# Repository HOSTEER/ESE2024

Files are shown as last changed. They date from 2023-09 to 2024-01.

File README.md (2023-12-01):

# ESE2024
    Emilie Butruille
    Louis Liénart
    Théo Césari
    Victor Lesne
------

Activer doxygen dans les propriétés du projet -> général C/C++, tuto doxygen https://www.youtube.com/watch?v=GC9Xy7nLxyw

Pour importer un projet sur cubeIDE, il faut faire "File" -> "Import" -> "General" -> "Project from Folder or Archive" puis sélectionner le directory (exemple "C:\Users\louis\Desktop\ProjetCubeIDE") et ensuite faire "finish".
Après ça, il faut régénérer des fichiers du code, donc cliquer sur "Device configuration tool Code generation"

Avec GitBash, pour retirer un fichier "add" par erreur faire un "git reset nom_du_fichier", un reset seul retirera tout les add fait.

Convention à avoir pour le stockage des sources :
pour stocker les lib créer faire un dossier source "Prod" avec comme sous-fichier "Inc" et "Src"
Ensuite les ajouter dans "Project" -> "Properties" -> "C/C++ General" -> "Paths and Symbols" -> "add" -> entrer "Prod/Inc" et faire ok.

Pour vérifier qu'une branch est ok, cloner un 2nd repo de la branch et la tester pour vérifier l'absence d'erreurs, sinon ça veut dire qu'il manque un truc au commit.

Ensuite il faut résoudre les conflits entre .cproject ( globalement garder le code du main ); .ioc (globalement fusionner les pins ajoutés et faire gaffe au pin, en double) et enfin le main.c ( où il faut fusionner )

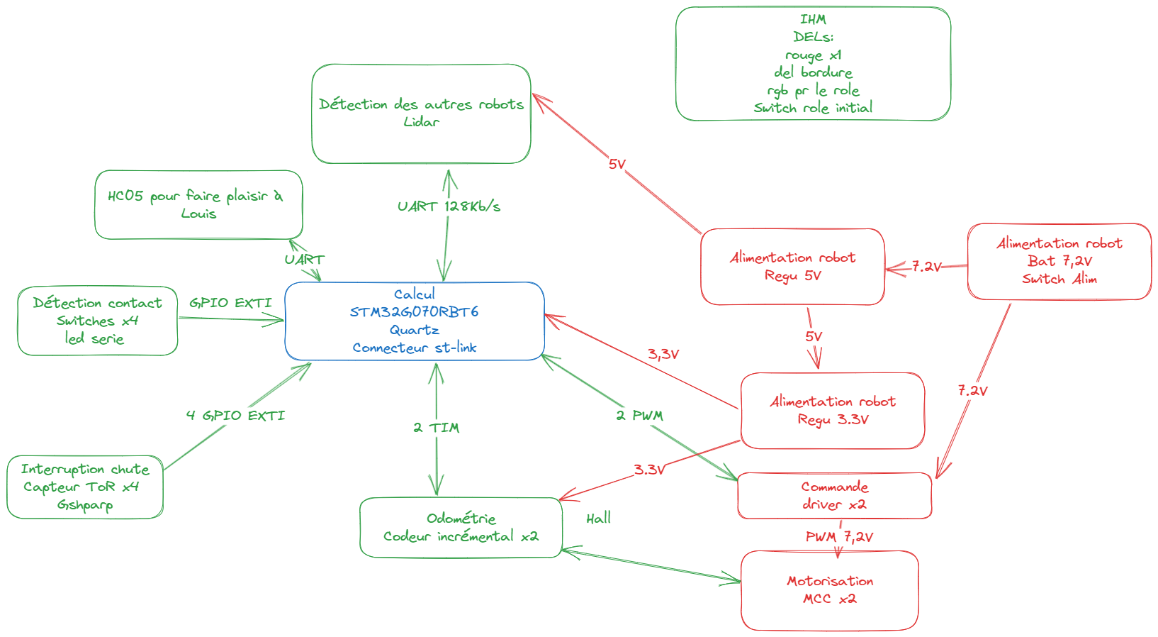
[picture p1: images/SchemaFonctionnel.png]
Schema fonctionnel du robot chat


conso moyenne 300 mA

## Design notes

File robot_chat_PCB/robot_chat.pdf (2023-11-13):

robot_chat

Ref | Qnty Value
C302, | 1 470uF
D201, D202, D203, D204, D205, D206, | 6 ~
D301, | 1 ~
D302, | 1 1N4148
D303, D304, D602 | 3 3.3V, 5V, Status
D501, D604, D605 | 3 Bump, Debug_1, Debug_2
D601, D603 | 2 Border_Detect, Error
F301, | 1 10A
IC401, IC402, | 2 NCS199A3RSQT2G
J301, J501 | 2 Bat,Bump
J401, J402 | 2 L_Mot,R_Mot
J502, | 1 Lidar
J503, J504 | 2 B_Detect, F_Detect
J601, | 1 BT
L201, | 1 2.2u
L301, | 1 4.7uH
SW201, SW601, SW602 | 3 RST, Start, Status
SW301, | 1 SW_SPDT_MSM
U201, | 1 STM32G070RBTx
U301, | 1 MP1475DJ-LF-P
U302, | 1 MIC5317-3.3xM5
U401, U402, | 2 ZXBM5210-SP
U501, | 1 LSM6DSM
Y201, | 1 16MHz

Footprint | ref farnell

Capacitor_SMD:CP_Elec_10x10.5

Diode_SMD:D_SOD-923 | 3702487RL
Diode_SMD:D_SMB | 3373187RL

Diode_SMD:D_SOD-323F

LED_SMD:LED_0603_1608Metric | 3796304
LED_SMD:LED_0603_1608Metric | 3796315
LED_SMD:LED_0603_1608Metric | 3796316
Fuse:Fuse_1206_3216Metric | 3564732
Package_TO_SOT_SMD:SOT-363_SC-70-6 | 2981170
Connector_JST:JST_XH_S2B-XH-A_1x02_P2.50mm_Horizontal | 1516289
Connector_JST:JST_XH_S6B-XH-A_1x06_P2.50mm_Horizontal | 1516294
Connector_JST:JST_XH_S8B-XH-A_1x08_P2.50mm_Horizontal | 1516296
Connector_JST:JST_XH_S3B-XH-A_1x03_P2.50mm_Horizontal | 1516290
Connector_PinSocket_2.54mm:PinSocket_1x06_P2.54mm_Horizontal | 2827951
Inductor_SMD:L_0603_1608Metric | 3666006

Inductor_SMD:L_1008_2520Metric

Button_Switch_SMD:SW_SPST_B3U-1000P | 1333652
472121020421:Toggle_Switch | 4244949

Package_QFP:LQFP-64_10x10mm_P0.5mm

Package_TO_SOT_SMD:TSOT-23-8

Package_TO_SOT_SMD:SOT-23-5

Package_SO:SOIC-8-1EP_3.9x4.9mm_P1.27mm_EP2.62x3.51mm_ThermalVias

Package_LGA:LGA-14_3x2.5mm_P0.5mm_LayoutBorder3x4y | 2664522

Crystal:Crystal_SMD_EuroQuartz_MT-4Pin_3.2x2.5mm

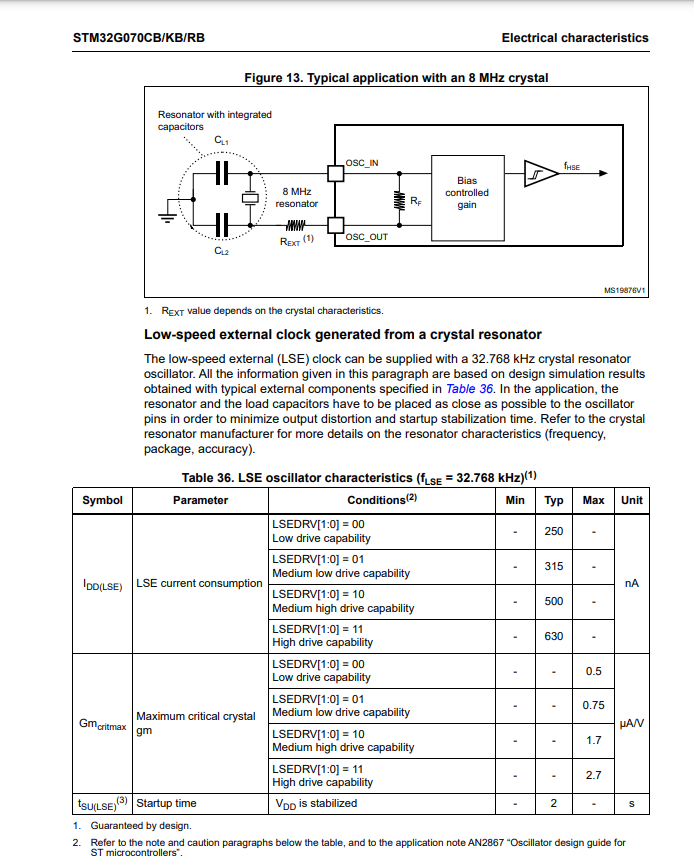
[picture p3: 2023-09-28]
Datasheets/quartz.PNG

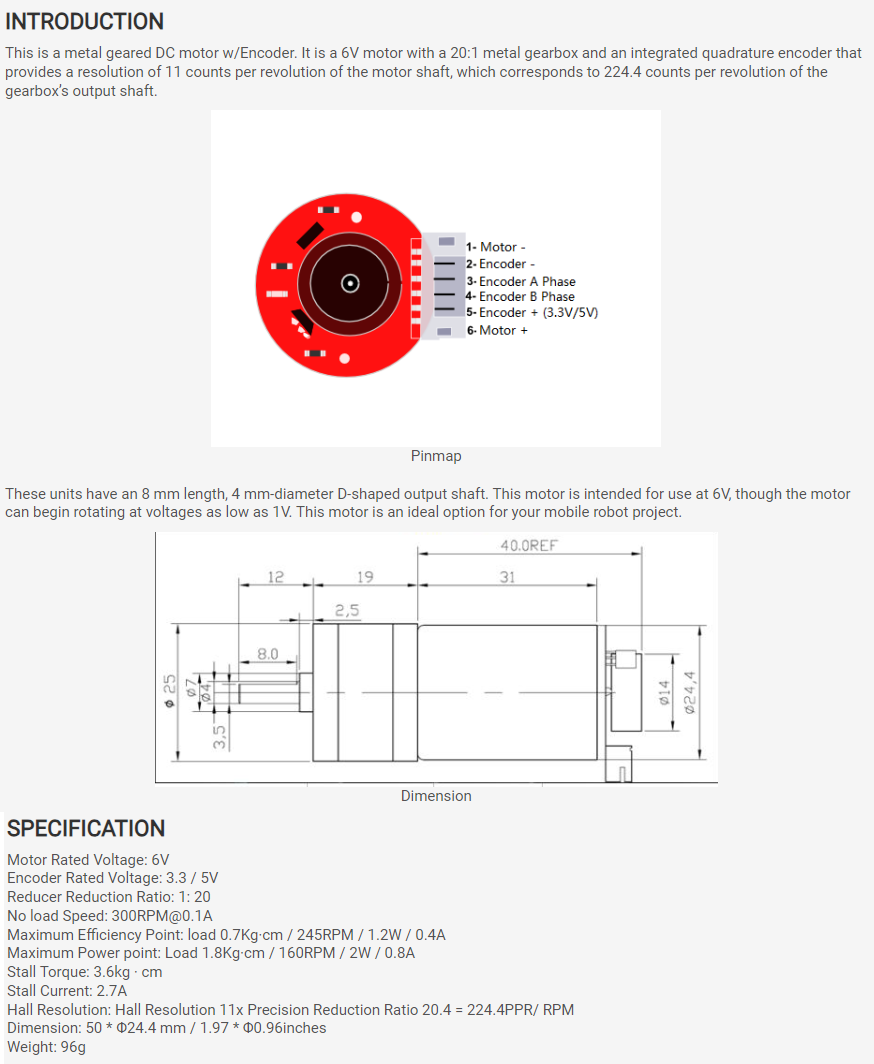
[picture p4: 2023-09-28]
Datasheets/DfRobot FIT0520.png

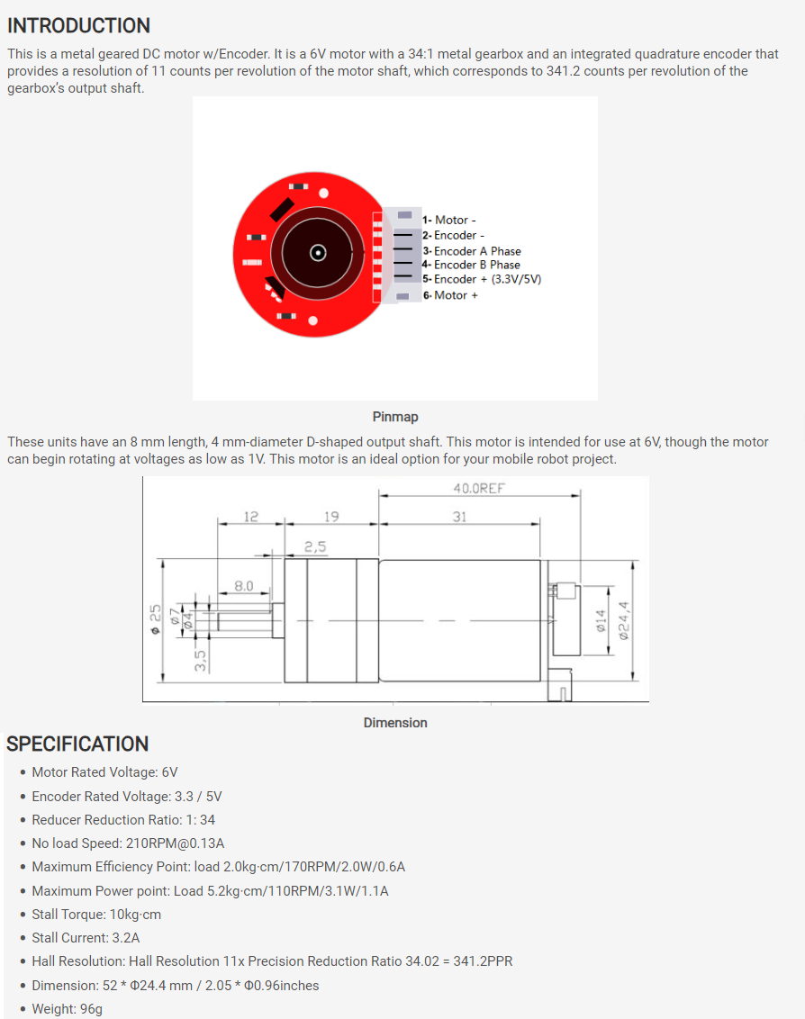
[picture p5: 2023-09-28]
Datasheets/DfRobot FIT0521.png

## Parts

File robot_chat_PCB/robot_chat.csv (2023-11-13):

Ref | Qnty | Value | Footprint | ref farnell
C302, | 1 | 470uF | Capacitor_SMD:CP_Elec_10x10.5
D201, D202, D203, D204, D205, D206, | 6 | ~ | Diode_SMD:D_SOD-923 | 3702487RL
D301, | 1 | ~ | Diode_SMD:D_SMB | 3373187RL
D302, | 1 | 1N4148 | Diode_SMD:D_SOD-323F
D303, D304, D602 | 3 | 3.3V, 5V, Status | LED_SMD:LED_0603_1608Metric | 3796304
D501, D604, D605 | 3 | Bump, Debug_1, Debug_2 | LED_SMD:LED_0603_1608Metric | 3796315
D601, D603 | 2 | Border_Detect, Error | LED_SMD:LED_0603_1608Metric | 3796316
F301, | 1 | 10A | Fuse:Fuse_1206_3216Metric | 3564732
IC401, IC402, | 2 | NCS199A3RSQT2G | Package_TO_SOT_SMD:SOT-363_SC-70-6 | 2981170
J301, J501 | 2 | Bat,Bump | Connector_JST:JST_XH_S2B-XH-A_1x02_P2.50mm_Horizontal | 1516289
J401, J402 | 2 | L_Mot,R_Mot | Connector_JST:JST_XH_S6B-XH-A_1x06_P2.50mm_Horizontal | 1516294
J502, | 1 | Lidar | Connector_JST:JST_XH_S8B-XH-A_1x08_P2.50mm_Horizontal | 1516296
J503, J504 | 2 | B_Detect, F_Detect | Connector_JST:JST_XH_S3B-XH-A_1x03_P2.50mm_Horizontal | 1516290
J601, | 1 | BT | Connector_PinSocket_2.54mm:PinSocket_1x06_P2.54mm_Horizontal | 2827951
L201, | 1 | 2.2u | Inductor_SMD:L_0603_1608Metric | 3666006
L301, | 1 | 4.7uH | Inductor_SMD:L_1008_2520Metric
SW201, SW601, SW602 | 3 | RST, Start, Status | Button_Switch_SMD:SW_SPST_B3U-1000P | 1333652
SW301, | 1 | SW_SPDT_MSM | 472121020421:Toggle_Switch | 4244949
U201, | 1 | STM32G070RBTx | Package_QFP:LQFP-64_10x10mm_P0.5mm
U301, | 1 | MP1475DJ-LF-P | Package_TO_SOT_SMD:TSOT-23-8
U302, | 1 | MIC5317-3.3xM5 | Package_TO_SOT_SMD:SOT-23-5
U401, U402, | 2 | ZXBM5210-SP | Package_SO:SOIC-8-1EP_3.9x4.9mm_P1.27mm_EP2.62x3.51mm_ThermalVias
U501, | 1 | LSM6DSM | Package_LGA:LGA-14_3x2.5mm_P0.5mm_LayoutBorder3x4y | 2664522
Y201, | 1 | 16MHz | Crystal:Crystal_SMD_EuroQuartz_MT-4Pin_3.2x2.5mm

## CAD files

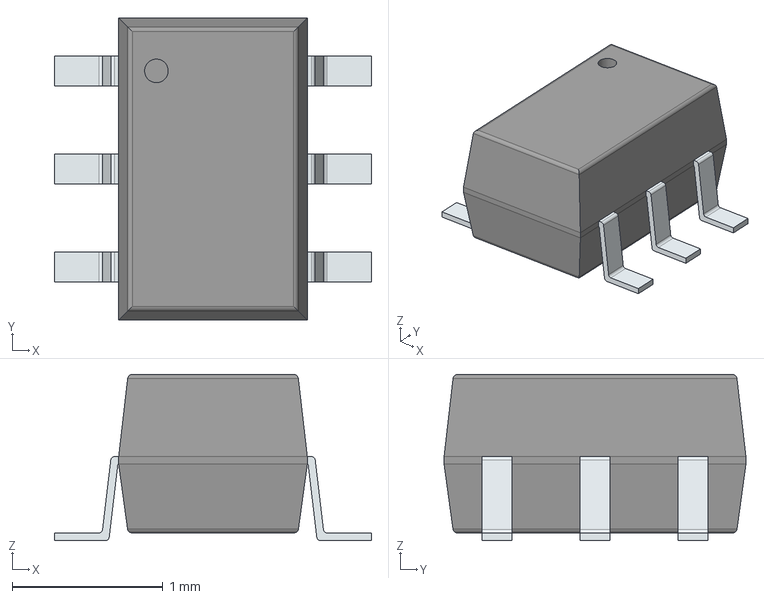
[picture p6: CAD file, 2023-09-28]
robot_chat_PCB/NCS199A3RSQT2G/NCS199A3RSQT2G.stp
2.10 x 2.00 x 1.10 mm
PinsArrayLR

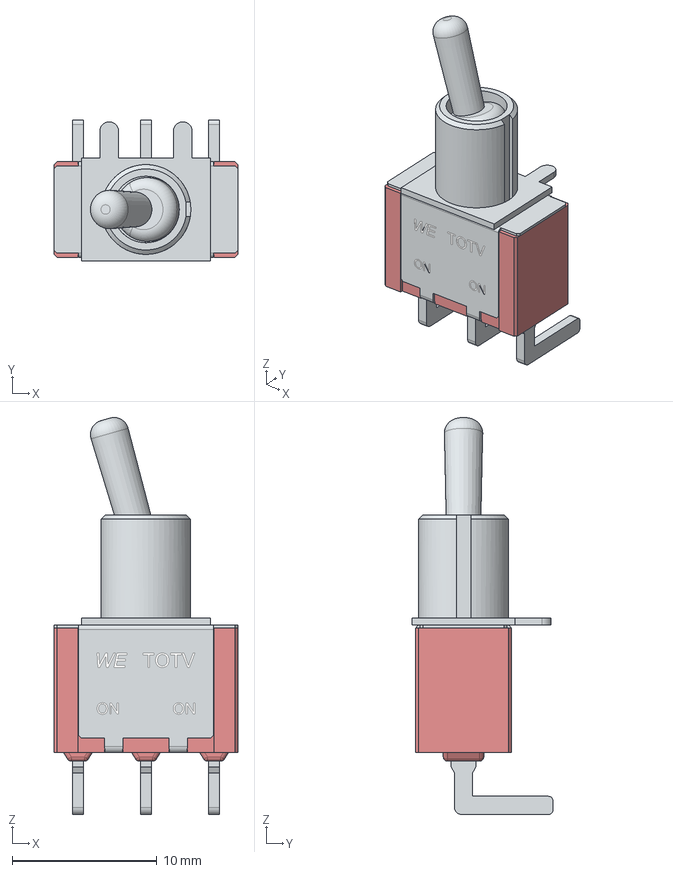
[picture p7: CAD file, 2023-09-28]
robot_chat_PCB/Toggle_Switch_472121020421/STP_472 121 020 421 (rev1).stp
12.7 x 9.72 x 27.4 mm
Base
Shielding
Switch
Pin x 3
Glue x 3
Shielding2

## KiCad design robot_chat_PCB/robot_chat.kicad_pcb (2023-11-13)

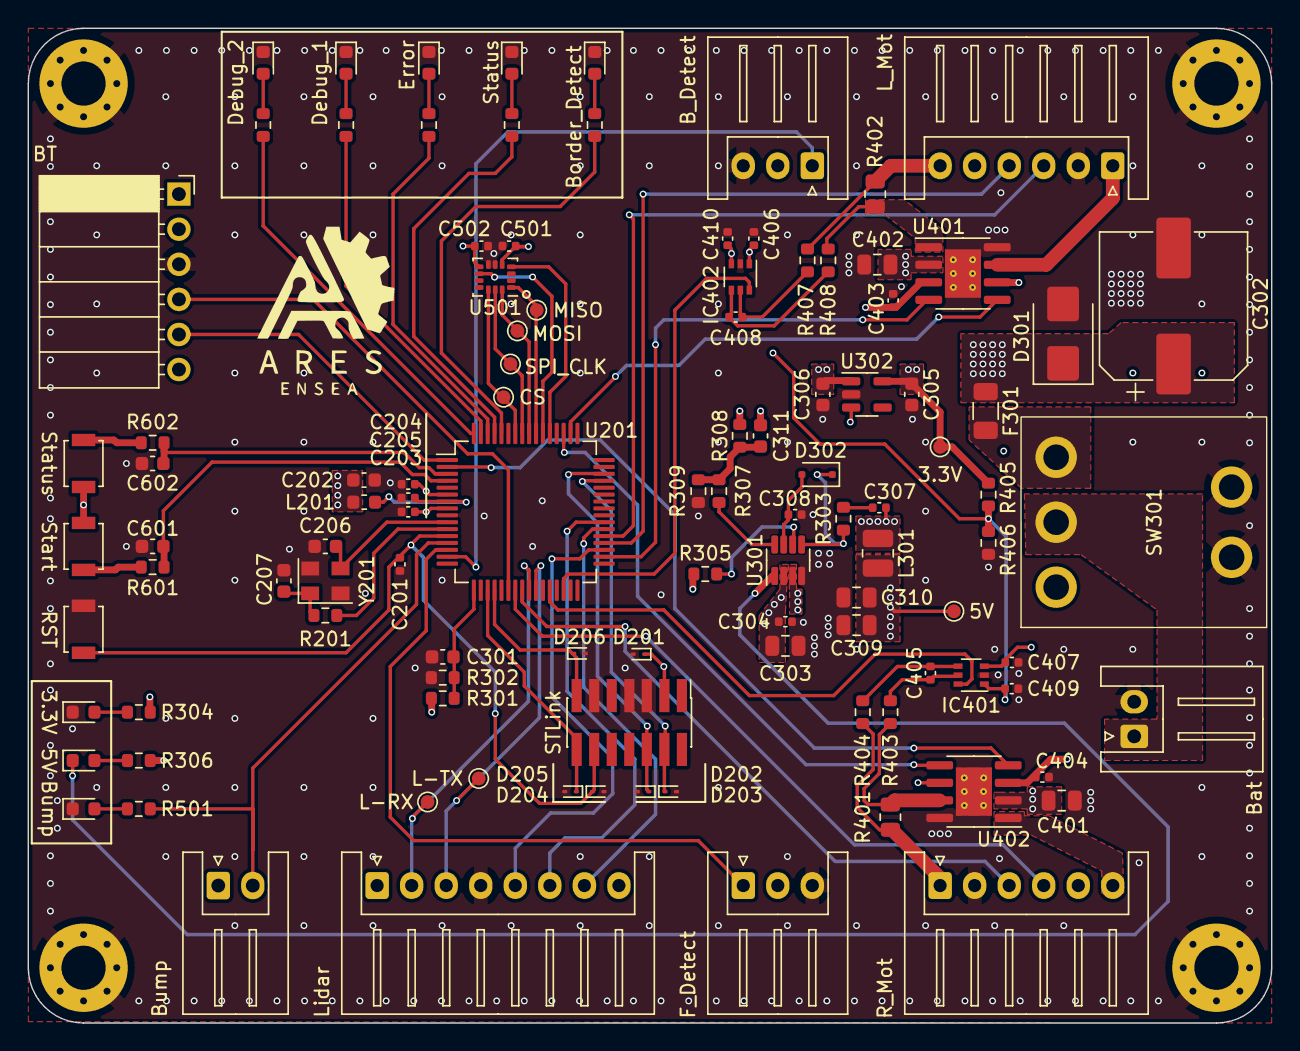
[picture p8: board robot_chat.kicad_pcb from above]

Board: 4 copper layers, 90.0 x 72.0 mm, 111 parts (0 on the bottom side), 78 nets.

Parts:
+3V301: 3.3V; TestPoint_Pad_D1.0mm
+5V301: 5V; TestPoint_Pad_D1.0mm
C201, C203, C204, C205, C403, C404, C405, C406, C407, C408, C409, C410: 0.1uF; C_0402_1005Metric
C202: 4.7uF; C_0603_1608Metric
C206, C207: 10p; C_0603_1608Metric
C301, C305, C306, C601, C602: 1uF; C_0603_1608Metric
C302: 470uF; CP_Elec_10x10.5
C303, C309, C310, C401, C402: 22uF; C_0805_2012Metric
C304, C307, C308: 0,1uF; C_0402_1005Metric
C311: 15pF; C_0603_1608Metric
C501, C502: 0.1u; C_0402_1005Metric
CS201: CS; TestPoint_Pad_D1.0mm
D201, D202, D203, D204, D205, D206: D_SOD-923
D301: D_SMB
D302: 1N4148; D_SOD-323F
D303: 3.3V; LED_0603_1608Metric
D304: 5V; LED_0603_1608Metric
D501: Bump; LED_0603_1608Metric
D601: Border_Detect; LED_0603_1608Metric
D602: Status; LED_0603_1608Metric
D603: Error; LED_0603_1608Metric
D604: Debug_1; LED_0603_1608Metric
D605: Debug_2; LED_0603_1608Metric
F301: 10A; Fuse_1206_3216Metric
H101, H102, H103, H104: MountingHole_Pad; MountingHole_3.2mm_M3_Pad_Via
IC401, IC402: NCS199A3RSQT2G; SOT-363_SC-70-6
J201: STLink; PinHeader_2x07_P1.27mm_Vertical_SMD
J301: Bat; JST_XH_S2B-XH-A_1x02_P2.50mm_Horizontal
J401: L_Mot; JST_XH_S6B-XH-A_1x06_P2.50mm_Horizontal
J402: R_Mot; JST_XH_S6B-XH-A_1x06_P2.50mm_Horizontal
J501: Bump; JST_XH_S2B-XH-A_1x02_P2.50mm_Horizontal
J502: Lidar; JST_XH_S8B-XH-A_1x08_P2.50mm_Horizontal
J503: B_Detect; JST_XH_S3B-XH-A_1x03_P2.50mm_Horizontal
J504: F_Detect; JST_XH_S3B-XH-A_1x03_P2.50mm_Horizontal
J601: BT; PinSocket_1x06_P2.54mm_Horizontal
L201: 2.2u; L_0603_1608Metric
L301: 4.7uH; L_1008_2520Metric
LIDAR_RX201: L-RX; TestPoint_Pad_D1.0mm
LIDAR_TX201: L-TX; TestPoint_Pad_D1.0mm
R201, R403, R404, R407, R408: 10R; R_0603_1608Metric
R301: 22k; R_0603_1608Metric
R302: 10k; R_0603_1608Metric
R303: 20; R_0603_1608Metric
R304, R306, R501, R601, R602, R603, R604, R605, R606, R607: 1k; R_0603_1608Metric
R305, R405, R406: 100k; R_0603_1608Metric
R307: 16k; R_0603_1608Metric
R308: 40.2k; R_0603_1608Metric
R309: 7.68k; R_0603_1608Metric
R401, R402: 0.015; R_0805_2012Metric
SDI201: MOSI; TestPoint_Pad_D1.0mm
SDO201: MISO; TestPoint_Pad_D1.0mm
SPI_CLK201: SPI_CLK; TestPoint_Pad_D1.0mm
SW201: RST; SW_SPST_B3U-1000P
SW301: SW_SPDT_MSM; Toggle_Switch
SW601: Start; SW_SPST_B3U-1000P
SW602: Status; SW_SPST_B3U-1000P
U201: STM32G070RBTx; LQFP-64_10x10mm_P0.5mm
U301: MP1475DJ-LF-P; TSOT-23-8
U302: MIC5317-3.3xM5; SOT-23-5
U401, U402: ZXBM5210-SP; SOIC-8-1EP_3.9x4.9mm_P1.27mm_EP2.62x3.51mm_ThermalVias
U501: LSM6DSM; LGA-14_3x2.5mm_P0.5mm_LayoutBorder3x4y
Y201: 16MHz; Crystal_SMD_EuroQuartz_MT-4Pin_3.2x2.5mm

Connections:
+3.3V: +3V301.1, C202.1, C203.1, C204.1, C305.1, C403.1, C404.1, C407.1, C410.1, C501.1, C502.1, D201.1 (A1), IC401.3 (VS), IC402.3 (VS), J201.3, J401.5, J402.5, J501.1, J503.2, J504.2, L201.1, R304.2, R405.1, SW601.2, SW602.2, U201.6 (VBAT), U201.8 (VDD), U302.5 (VOUT), U401.3 (VDD), U401.6 (VREF), U402.3 (VDD), U402.6 (VREF), U501.5 (VDDIO), U501.8 (VDD)
+5V: +5V301.1, C306.1, C309.1, C310.1, C311.2, J502.1, J601.2, L301.2, R306.1, R308.2, U302.1 (VIN), U302.3 (EN)
+7.5V: C302.1, C303.1, C304.1, C401.1, C402.1, D301.1 (A1), F301.1, R301.1, R305.1, U301.2 (IN), U401.2 (VM), U402.2 (VM)
/HMI/BT_RX: J601.5, U201.1 (PC11)
/HMI/BT_TX: J601.4, U201.22 (PA5)
/HMI/PB_GAME_START: C601.1, R601.1, U201.4 (PC14)
/HMI/PB_GAME_STATUS: C602.1, R602.1, U201.3 (PC13)
/Motor drivers/ENCODER_L_A: J401.3, U201.37 (PA9/NC)
/Motor drivers/ENCODER_L_B: J401.4, U201.36 (PA8)
/Motor drivers/ENCODER_R_A: J402.3, U201.24 (PA7)
/Motor drivers/ENCODER_R_B: J402.4, U201.23 (PA6)
/Motor drivers/FWD_L: U201.34 (PB14), U401.4 (FWD)
/Motor drivers/FWD_R: U201.2 (PC12), U402.4 (FWD)
/Motor drivers/IN_L+: C408.2, IC402.4 (IN+), R408.2
/Motor drivers/IN_L-: C408.1, IC402.5 (IN-), R407.2
/Motor drivers/IN_R+: C405.2, IC401.4 (IN+), R404.2
/Motor drivers/IN_R-: C405.1, IC401.5 (IN-), R403.2
/Motor drivers/I_READ_L: IC402.6 (OUT), U201.30 (PB10)
/Motor drivers/I_READ_R: IC401.6 (OUT), U201.28 (PB1)
/Motor drivers/MOTOR_L+: J401.1, U401.7 (OUT2)
/Motor drivers/MOTOR_L-: R402.2, R408.1, U401.1 (OUT1)
/Motor drivers/MOTOR_R+: R401.2, R403.1, U402.7 (OUT2)
/Motor drivers/MOTOR_R-: J402.6, U402.1 (OUT1)
/Motor drivers/REV_L: U201.50 (PD0), U401.5 (REV)
/Motor drivers/REV_R: U201.51 (PD1), U402.5 (REV)
/Motor drivers/RSENSE_L-: J401.6, R402.1, R407.1
/Motor drivers/RSENSE_R-: J402.1, R401.1, R404.1
/Motor drivers/VREF: C406.1, C409.1, IC401.1 (REF), IC402.1 (REF), R405.2, R406.1
/Power Supply/BST: D302.1 (K), R303.1, U301.5 (BST)
/Power Supply/EN/SYNC: R305.2, U301.6 (EN/SYNC)
/Power Supply/FB: R307.1, U301.8 (FB)
/Power Supply/PG: D304.1 (K), U301.1 (PG)
/Power Supply/SW: C307.2, L301.1, U301.3 (SW)
/Power Supply/VBAT_READ: C301.2, R301.2, R302.1, U201.17 (PA0)
/Power Supply/VCC: C308.1, D302.2 (A), U301.7 (VCC)
/STM/BACK_BORDER_DETECT: J503.1, U201.15 (PC2)
/STM/BUMPER_SW: J501.2, R501.2, U201.13 (PC0)
/STM/FRONT_BORDER_DETECT: J504.1, U201.14 (PC1)
/STM/IMU_INT1: U201.53 (PD3), U501.4 (INT1)
/STM/IMU_INT2: U201.54 (PD4), U501.9 (INT2)
/STM/IMU_SPI_CLK: SPI_CLK201.1, U201.57 (PB3), U501.13 (SCL)
/STM/IMU_SPI_CS: CS201.1, U201.58 (PB4), U501.12 (CS)
/STM/IMU_SPI_SDI: SDI201.1, U201.56 (PD6), U501.14 (SDA)
/STM/IMU_SPI_SDO: SDO201.1, U201.55 (PD5), U501.1 (SDO/SA0)
/STM/LIDAR_EN: J502.7, U201.38 (PC6)
/STM/LIDAR_RANGING_EN: J502.6, U201.39 (PC7)
/STM/LIDAR_RX: J502.2, LIDAR_RX201.1, U201.25 (PC4)
/STM/LIDAR_SPEED: J502.5, U201.35 (PB15)
/STM/LIDAR_TX: J502.3, LIDAR_TX201.1, U201.26 (PC5)
/STM/QUARTZ_0: C206.2, U201.10 (PF0), Y201.3
/STM/QUARTZ_1: R201.2, U201.11 (PF1)
/STM/STLINK_RX: D206.1 (A1), J201.13, U201.20 (PA3)
/STM/STLINK_TX: D205.1 (A1), J201.14, U201.19 (PA2)
/STM/SWCLK: D203.1 (A1), J201.6, U201.46 (PA14)
/STM/SWDIO: D202.1 (A1), J201.4, U201.45 (PA13)
/STM/VREF+: C205.2, L201.2, U201.7 (VREF+)
/STM/~RST: C201.2, D204.1 (A1), J201.12, SW201.2, U201.12 (NRST)
GND: C201.1, C202.2, C203.2, C204.2, C205.1, C206.1, C207.1, C301.1, C302.2, C303.2, C304.2, C305.2, C306.2, C308.2, C309.2, C310.2, C401.2, C402.2, C403.2, C404.2, C406.2, C407.2, C409.2, C410.2, C501.2, C502.2, C601.2, C602.2, D201.2 (A2), D202.2 (A2), D203.2 (A2), D204.2 (A2), D205.2 (A2), D206.2 (A2), D301.2 (A2), D303.1 (K), D501.1 (K), D601.1 (K), D602.1 (K), D603.1 (K), D604.1 (K), D605.1 (K), H101.1, H102.1, H103.1, H104.1, IC401.2 (GND), IC402.2 (GND), J201.5, J201.7, J201.11, J301.2, J401.2, J402.2, J502.4, J503.3, J504.3, J601.3, R302.2, R309.2, R406.2, SW201.1, SW301.4, SW301.5, U201.9 (VSS), U301.4 (GND), U302.2 (GND), U401.8 (GND), U401.9 (GND), U402.8 (GND), U402.9 (GND), U501.6 (GND), U501.7 (GND), Y201.2, Y201.4
unnamed: C207.2, R201.1, Y201.1
unnamed: C307.1, R303.2
unnamed: C311.1, R307.2, R308.1, R309.1
unnamed: D303.2 (A), R304.1
unnamed: D304.2 (A), R306.2
unnamed: D501.2 (A), R501.1
unnamed: D601.2 (A), R603.2
unnamed: D602.2 (A), R604.2
unnamed: D603.2 (A), R605.2
unnamed: D604.2 (A), R606.2
unnamed: D605.2 (A), R607.2
unnamed: F301.2, SW301.1
unnamed: J301.1, SW301.2
unnamed: R601.2, SW601.1
unnamed: R602.2, SW602.1
USER_LED_0: R603.1, U201.60 (PB6)
USER_LED_1: R604.1, U201.61 (PB7)
USER_LED_2: R605.1, U201.62 (PB8)
USER_LED_3: R606.1, U201.63 (PB9)
USER_LED_4: R607.1, U201.64 (PC10)

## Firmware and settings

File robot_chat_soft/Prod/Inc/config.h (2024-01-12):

/*
 * config.h
 *
 *  Created on: Dec 14, 2023
 *      Author: les_victor
 */

#ifndef INC_CONFIG_H_
#define INC_CONFIG_H_

//Pour retirer toutes les autres tâches
//#define DEV_MODE

//Stratégie
#define VITESSE_CIRCUIT 100
#define VITESSE_CORRECTION 2
#define CHAMP_VECT_MARGE 50
#define HAUTEUR_CHAMP 300
#define LARGEUR_CHAMP 500

#define DEFAULT_STRAT_MODE PREY | TURN_TRIGO

//Asserv
#define DEFAULT_SPEED 150


#define MATCH_LENGTH 30

#define COLLISION_TIMEOUT 3000

#endif /* INC_CONFIG_H_ */

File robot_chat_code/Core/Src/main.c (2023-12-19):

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
/* Includes ------------------------------------------------------------------*/
#include "main.h"
#include "cmsis_os.h"
#include "adc.h"
#include "dma.h"
#include "spi.h"
#include "tim.h"
#include "usart.h"
#include "gpio.h"

/* USER CODE BEGIN Includes */
#include <stdio.h>
#include <string.h>
#include "ydlidar_x4.h"
#include "imu.h"
#include "motor.h"
#include "fixpoint_math.h"
#include "control.h"
#include "odometry.h"
#include "trajectoire.h"
/* USER CODE END Includes */

/* USER CODE BEGIN PTD */
typedef enum{
	HUNTER			= 0x10,
	PREY			= 0x20,
	FALL_FORWARD 	= 0x00,
	FALL_BACKWARD 	= 0x01,
	COLL_FRONT 		= 0x02,
	COLL_BACK 		= 0x03,
	COLL_LEFT 		= 0x04,
	COLL_RIGHT 		= 0x05
}strat_mode_t;
/* USER CODE END PTD */

/* USER CODE BEGIN PD */
#define QUEUE_PRINTF_SIZE 100
#define QUEUE_PRINTF_LENGTH 10
#define DEFAULT_STACK_SIZE 512
#define DEFAULT_TASK_PRIORITY 1
#define DEFAULT_LIDAR_SPEED 950
#define TRUNC_FIXP 1000000000000

#define WHEEL_DIAMETER (43<<24) 	//43mm diameter, Q8.24
#define WHEEL_DIST (153<<16) 		//153mm distance between wheels, Q16.16
#define ENC_TICKSPERREV (400<<16)		//400 encoder ticks per revolution, Q16.16
#define ODOMETRY_FREQ 50 			//50Hz odometry refresh frequency
#define ROBOT_SPEED (500<<16) 		//robot speed, mm/s Q16.16
/* USER CODE END PD */


/* USER CODE BEGIN PV */
QueueHandle_t q_printf = NULL;

TaskHandle_t h_task_init = NULL;
TaskHandle_t h_IMU_taskRead = NULL;
TaskHandle_t h_printf = NULL;
TaskHandle_t h_task_lidar = NULL;
TaskHandle_t h_task_lidar_ISR = NULL;
TaskHandle_t h_task_BT_and_Wire_RX_ISR = NULL;
TaskHandle_t h_task_BTN_ISR = NULL;
TaskHandle_t h_task_Motor = NULL;
TaskHandle_t h_task_MotorSpeed = NULL;

SemaphoreHandle_t lidar_RX_semaphore;
SemaphoreHandle_t Wire_BT_RX_semaphore;
SemaphoreHandle_t BTN_STATUS_semaphore;

BaseType_t ret;
h_ydlidar_x4_t lidar;
h_imu_drv_t h_imu;
uint8_t BT_RX;
uint8_t rx_pc;
uint8_t string_display[720];
hMotor_t Rmot;
hMotor_t Lmot;
hOdometry_t hOdometry;
int32_t mot_speed = 0;
int16_t cnt = 0;
int32_t angle = 0;
uint8_t odom_overflow = 0;
//vector_t test_vect = {-1*(2<<16),1<<16};
strat_mode_t strat_mode = PREY;
/* USER CODE END PV */

void SystemClock_Config(void);
void MX_FREERTOS_Init(void);
/* USER CODE BEGIN PFP */
int __io_putchar(int ch)
{
	HAL_UART_Transmit(&huart2, (uint8_t *)&ch, 1, HAL_MAX_DELAY);
	HAL_UART_Transmit(&huart3, (uint8_t *)&ch, 1, HAL_MAX_DELAY);
	return ch;
}

void HAL_UART_RxCpltCallback(UART_HandleTypeDef * huart){
	if(huart->Instance == USART1){
		BaseType_t xHigherPriorityTaskToken = pdFALSE;
		xSemaphoreGiveFromISR(lidar_RX_semaphore, &xHigherPriorityTaskToken);
		portYIELD_FROM_ISR(xHigherPriorityTaskToken);
	}
	else if(huart->Instance == USART3 || huart->Instance == USART2){
		BaseType_t xHigherPriorityTaskToken = pdFALSE;
		xSemaphoreGiveFromISR(Wire_BT_RX_semaphore, &xHigherPriorityTaskToken);
		portYIELD_FROM_ISR(xHigherPriorityTaskToken);
	}
}

void HAL_UART_RxHalfCpltCallback(UART_HandleTypeDef *huart)
{
	if(huart->Instance == USART1){
		BaseType_t xHigherPriorityTaskToken = pdFALSE;
		xSemaphoreGiveFromISR(lidar_RX_semaphore, &xHigherPriorityTaskToken);
		portYIELD_FROM_ISR(xHigherPriorityTaskToken);
	}
}

int lidar_uart_transmit(uint8_t *p_data, uint16_t size)
{
	HAL_UART_Transmit(&huart1,p_data, size, HAL_MAX_DELAY);
	return 0;
}

int lidar_uart_receive(uint8_t *p_data)
{
	HAL_UART_Receive_DMA(&huart1,p_data, LIDAR2DMA_SIZE);
	return 0;
}

void HAL_GPIO_EXTI_Rising_Callback(uint16_t GPIO_Pin)
{
	if(GPIO_Pin == GPIO_PIN_13) {
		BaseType_t xHigherPriorityTaskToken = pdFALSE;
		xSemaphoreGiveFromISR(BTN_STATUS_semaphore, &xHigherPriorityTaskToken);
		portYIELD_FROM_ISR(xHigherPriorityTaskToken);
	}

	if(GPIO_Pin == FBD_EXTI1_Pin) {
		HAL_GPIO_WritePin(USER_LED3_GPIO_Port, USER_LED3_Pin, 1);
	}
	if(GPIO_Pin == BBD_EXTI2_Pin) {
		HAL_GPIO_WritePin(USER_LED3_GPIO_Port, USER_LED3_Pin, 1);
	}
}

void HAL_GPIO_EXTI_Falling_Callback(uint16_t GPIO_Pin){
	if(GPIO_Pin == FBD_EXTI1_Pin) {
		HAL_GPIO_WritePin(USER_LED3_GPIO_Port, USER_LED3_Pin, 0);
	}
	if(GPIO_Pin == BBD_EXTI2_Pin) {
		HAL_GPIO_WritePin(USER_LED3_GPIO_Port, USER_LED3_Pin, 0);
	}
}


void task_init(void * unused)
{

	printf("Task init ok\r\n");
	for(;;){
		//imu_dev(&h_imu);
		//printf("Task init looping\r\n");
		HAL_GPIO_TogglePin(USER_LED0_GPIO_Port, USER_LED0_Pin);
		//HAL_GPIO_TogglePin(USER_LED1_GPIO_Port, USER_LED1_Pin);
		//HAL_GPIO_TogglePin(USER_LED2_GPIO_Port, USER_LED2_Pin);
		//HAL_GPIO_TogglePin(USER_LED3_GPIO_Port, USER_LED3_Pin);
		//HAL_GPIO_TogglePin(USER_LED4_GPIO_Port, USER_LED4_Pin);
		vTaskDelay(1000);
	}
}

void IMU_taskRead(void * unused)
{
	uint8_t msg [QUEUE_PRINTF_SIZE];
	uint32_t time_lapped;

	for(;;){
		//printf("Task init looping\r\n");
		time_lapped = __HAL_TIM_GET_COUNTER(&htim7);
		//__HAL_TIM_SET_COUNTER(&htim7, 0);
		//HAL_TIM_Base_Start(&htim7);
		IMU_gyro(&h_imu);

		/*uint8_t gyro_addr = 0x11;
		uint8_t value[3];
		IMU_read8(&h_imu, gyro_addr, value);*/

		/*if(!odom_overflow){
			sprintf(msg, "Mesures de vitesse de rotation faite en %d us\r\n", time_lapped);
			xQueueSend(q_printf, (void *)msg, 5);
		}
		else{
			sprintf(msg, "Mesures de vitesse de rotation faite, mais la base de temps est corrompue (%d overflow(s))\r\n", odom_overflow);
			xQueueSend(q_printf, (void *)msg, 5);
		}*/


		//sprintf(msg, "Lecture des accelerations :\r\n- Gyro X :%d\r\n- Gyro Y :%d\r\n- Gyro Z :%d\r\n", h_imu.gyro[0],  h_imu.gyro[1], h_imu.gyro[2]);
		//xQueueSend(q_printf, (void *)msg, 5);

		//printf("Task init looping\r\n");
		//HAL_GPIO_TogglePin(USER_LED1_GPIO_Port, USER_LED1_Pin);
		vTaskDelay(5);
	}
}

void printfTask(void * unused)
{
	uint8_t msg[QUEUE_PRINTF_SIZE];
	BaseType_t ret;
	for(;;){
		ret = xQueueReceive(q_printf, (void *)msg, portMAX_DELAY);
		uint16_t msg_len = strlen(msg);
		if(ret == pdTRUE){
			//printf(msg);
			HAL_UART_Transmit_IT(&huart2, msg, msg_len);
		}
	}
}

void task_lidar(void * unused)
{
	printf("Task lidar ok\r\n");
	lidar.serial_drv.transmit = lidar_uart_transmit;
	lidar.serial_drv.receive = lidar_uart_receive;
	lidar.decode_state = SCANNING;
	lidar.serial_drv.receive(lidar.buf_DMA);
	lidar.nb_smpl = 0;
	lidar.start_angl = 0;
	lidar.end_angl = 0;
	HAL_GPIO_WritePin(LIDAR_RANGING_EN_GPIO_Port, LIDAR_RANGING_EN_Pin, GPIO_PIN_SET);
	HAL_GPIO_WritePin(LIDAR_EN_GPIO_Port, LIDAR_EN_Pin, GPIO_PIN_SET);
	HAL_TIM_PWM_Start(&htim15, TIM_CHANNEL_2);
	__HAL_TIM_SET_COMPARE(&htim15,TIM_CHANNEL_2, DEFAULT_LIDAR_SPEED-1);
	vTaskDelete(0);
	/*for(;;){
		if( xSemaphoreTake(lidar_RX_semaphore, 1000) == pdFALSE)
		{
			//HAL_NVIC_SystemReset();
		}
		ydlidar_x4_irq_cb(&lidar);
	}*/
}

void task_lidar_ISR(void * unused)
{
	printf("Task lidar ISR ok\r\n");
	for(;;){
		xSemaphoreTake(lidar_RX_semaphore, portMAX_DELAY );
		ydlidar_x4_irq_cb(&lidar);
		HAL_GPIO_TogglePin(USER_LED3_GPIO_Port, USER_LED3_Pin);
	}
}

void task_BT_and_Wire_RX_ISR(void * unused)
{
	printf("Task lidar ISR ok\r\n");
	HAL_UART_Receive_IT(&huart2, &rx_pc, 1);
	HAL_UART_Receive_IT(&huart3, &rx_pc, 1);
	for(;;){
		xSemaphoreTake(Wire_BT_RX_semaphore, portMAX_DELAY );
		if(rx_pc == 0xAA){
			rx_pc = 0xFF;
			for(int i=0;i<720;i++){
				if(i%2 == 0){
					string_display[i] = (lidar.sorted_dist[i>>1])>>8;
				}else{
					string_display[i] = (lidar.sorted_dist[i>>1]) & 0x00FF;
				}
			}
			HAL_UART_Transmit_DMA(&huart2,string_display, 720);
			HAL_UART_Transmit_DMA(&huart3,string_display, 720);
			HAL_UART_Receive_IT(&huart2, &rx_pc, 1);
			HAL_UART_Receive_IT(&huart3, &rx_pc, 1);
		}
		HAL_GPIO_TogglePin(USER_LED2_GPIO_Port, USER_LED2_Pin);
	}
}

void task_BTN_ISR(void * unused)
{
	printf("Task BTN ok\r\n");
	for(;;){
		xSemaphoreTake(BTN_STATUS_semaphore, portMAX_DELAY);
		ydlidar_x4_scan(&lidar);
		HAL_GPIO_TogglePin(USER_LED1_GPIO_Port, USER_LED1_Pin);
		//mot_speed ^= 1;
	}
}

void task_Motor(void * unused)
{
	vTaskDelay(10);
	motor_set_PWM(&Rmot, 0);
	motor_set_PWM(&Lmot, 0);
	Rmot.current_offset = Rmot.adc_dma_buff[Rmot.dma_buff_index];
	Lmot.current_offset = Lmot.adc_dma_buff[Lmot.dma_buff_index];
	int32_t speed = 0;
	int32_t angle = 0;
	uint32_t norm = 0;
	for(;;)
	{
		vTaskDelay(500);
		speed = Rmot.speed_measured[Rmot.speed_index];
		//CORDIC_vector(&test_vect);
		//angle = test_vect.angle*10;
		//norm = test_vect.norm*100;
		//printf("angle = %d, norme = %d\r\n", (int)angle/(1<<24), (int)norm/(1<<16));
		//printf("FWD %d\r\n",(int)(int16_t)__HAL_TIM_GET_COMPARE(Lmot.tim_FWD,TIM_CHANNEL_1));
		//printf("REV %d\r\n",(int)(int16_t)__HAL_TIM_GET_COMPARE(Lmot.tim_REV,TIM_CHANNEL_1));
		//printf("L Vdiff %d\r\n", (int)(fixed_div(Lmot.speed_output[Lmot.speed_index],128<<16,16) - fixed_div(Lmot.speed_measured[Lmot.speed_index],80<<16,16))/(1<<16));
		//printf("angle %d\r\n", (int)(hOdometry.angle*10/(1<<24)));
		//printf("dr %d\r\n", (int)(hOdometry.dr/(1<<24)));
		//printf("x %d, y %d\r\n", (int)hOdometry.x/(1<<16), (int)hOdometry.y/(1<<16));
		//printf("counts %d\r\n", (int)cnt);

		/*motor_set_PWM(&Rmot, 512);
		motor_set_PWM(&Lmot, 512);
		vTaskDelay(2000);
		motor_set_PWM(&Rmot, 0);
		motor_set_PWM(&Lmot, 0);
		vTaskDelay(2000);
		motor_set_PWM(&Rmot, -512);
		motor_set_PWM(&Lmot, -512);*/
	}
}

void task_MotorSpeed(void * unused)
{
	uint32_t V = 0;
	int32_t speed = 0;
	int32_t angle_corr = 0;
	int32_t Lspeed = 0;
	int32_t Rspeed = 0;
	for(;;)
	{
		//V = battery_get_voltage();
		cnt = (int16_t)__HAL_TIM_GET_COUNTER(Rmot.tim_ENC);
		odometry_update_pos(&hOdometry);
		//motor_get_speed(&Rmot);
		//motor_get_speed(&Lmot);
		//motor_get_current(&Rmot);
		//motor_get_current(&Lmot);
		if(hOdometry.x > 1000<<15)
		{
			angle += PI;
			hOdometry.x = 0;
		}
		if(hOdometry.y > 1000<<15)
		{
			angle += PI;
			hOdometry.y = 0;
			//mot_speed = 0;
		}
		if(hOdometry.x < -1000<<15)
		{
			angle += PI;
			hOdometry.x = 0;
		}
		if(hOdometry.y < -1000<<15)
		{
			angle += PI;
			hOdometry.y = 0;
			//mot_speed = 0;
		}
		if(angle > PI)
		{
			angle = -PI + angle%PI;
		}
		else if(angle < -PI)
		{
			angle = PI - angle%PI;
		}
		angle_corr = set_angle_corr(&hOdometry, angle);
		Rspeed = (int32_t)ROBOT_SPEED + fixed_mul((int32_t)ROBOT_SPEED, angle_corr, 24);
		Lspeed = (int32_t)ROBOT_SPEED - fixed_mul((int32_t)ROBOT_SPEED, angle_corr, 24);
		//speed = Rmot.speed_measured[Rmot.speed_index];
		//motor_set_PWM(&Rmot, 1024);
		//printf("vitesse moteur = %d.%u mm/s, courant moteur = %d.%u mA, tension batterie = %d.%u V\r\n", (int)(speed/(1<<16)), (unsigned int)conv_frac16_dec(speed & 0xFFFF,TRUNC_FIXP), (int)(Rmot.current_measured[Rmot.current_index]/(1<<16)), (unsigned int)conv_frac16_dec(Rmot.current_measured[Rmot.current_index] & 0xFFFF, TRUNC_FIXP) , (int)(V/(1<<16)),(unsigned int)conv_frac16_dec(V & 0xFFFF,TRUNC_FIXP));
		//printf("counts = %d, mesure : %d.%u mm/s, error : %d.%u mm/s, output : %d.%u, integral : %d.%u\r\n", (int)cnt, (int)(speed/(1<<16)), (unsigned int)conv_frac16_dec(speed & 0xFFFF, TRUNC_FIXP),(int)(Rmot.speed_error[Rmot.speed_index]/(1<<16)), (unsigned int)conv_frac16_dec((Rmot.speed_error[Rmot.speed_index]) & 0xFFFF, TRUNC_FIXP), (int)Rmot.speed_output[Rmot.speed_index]/(1<<16), (unsigned int)conv_frac16_dec(Rmot.speed_output[Rmot.speed_index] & 0xFFFF, TRUNC_FIXP), (int)(Rmot.speed_integral/(1<<16)), (unsigned int)conv_frac16_dec(Rmot.speed_integral & 0xFFFF, TRUNC_FIXP));
		set_speed_PID(&Rmot,mot_speed*Rspeed);	// 1<<14 = 150rpm , 1<<13 = 75rpm
		set_speed_PID(&Lmot,-(mot_speed*Lspeed));
		//printf("vitesse moteur = %d.%u rpm, courant moteur = %d.%u mA, tension batterie = %d.%u V\r\n", (int)(speed/(1<<16)), (unsigned int)conv_frac16_dec(speed & 0xFFFF,TRUNC_FIXP), (int)(Rmot.current_measured[Rmot.current_index]/(1<<16)), (unsigned int)conv_frac16_dec(Rmot.current_measured[Rmot.current_index] & 0xFFFF, TRUNC_FIXP) , (int)(V/(1<<16)),(unsigned int)conv_frac16_dec(V & 0xFFFF,TRUNC_FIXP));
		//printf("adc buffer 0: %d, 1: %d, 2: %d, i = %d, count = %d\r\n", (int)adcBuff[0],(int)adcBuff[1],(int)adcBuff[2], k, (int)__HAL_TIM_GET_COUNTER(&htim15));
		vTaskDelay(20);
	}
}

void fall_detection(void * unused){

}

/* USER CODE END PFP */

/**
  * @brief  The application entry point.
  * @retval int
  */
int main(void)
{
  /* MCU Configuration--------------------------------------------------------*/

  /* Reset of all peripherals, Initializes the Flash interface and the Systick. */
  HAL_Init();

  /* Configure the system clock */
  SystemClock_Config();

  /* Initialize all configured peripherals */
  MX_GPIO_Init();
  MX_DMA_Init();
  MX_ADC1_Init();
  MX_TIM1_Init();
  MX_TIM3_Init();
  MX_TIM14_Init();
  MX_TIM15_Init();
  MX_TIM16_Init();
  MX_TIM17_Init();
  MX_USART1_UART_Init();
  MX_USART2_UART_Init();
  MX_USART3_UART_Init();
  MX_SPI1_Init();
  MX_TIM7_Init();
  /* USER CODE BEGIN 2 */
	lidar_RX_semaphore = xSemaphoreCreateBinary();
	Wire_BT_RX_semaphore = xSemaphoreCreateBinary();
	BTN_STATUS_semaphore = xSemaphoreCreateBinary();
	//q_printf = xQueueCreate(QUEUE_PRINTF_LENGTH, QUEUE_PRINTF_SIZE);

	HAL_TIM_PWM_Start_IT(&htim15,TIM_CHANNEL_1 | TIM_CHANNEL_2);

	current_sense_start();

	motor_init(&Rmot, &htim17, &htim14, &htim3, 1, 5<<16, 1<<14, 0, 1023<<16, 10, 0, 0, 0, 0);
	motor_init(&Lmot, &htim15, &htim16, &htim1, 2, 5<<16, 1<<14, 0, 1023<<16, 10, 0, 0, 0, 0);

	odometry_init(&hOdometry, &Rmot, &Lmot, WHEEL_DIAMETER, ENC_TICKSPERREV, WHEEL_DIST, ODOMETRY_FREQ);

	ret = xTaskCreate(task_init, "task_init", DEFAULT_STACK_SIZE/2, NULL, DEFAULT_TASK_PRIORITY, &h_task_init);
	if(ret != pdPASS)
	{
		printf("Could not create task init \r\n");
		Error_Handler();
	}
	ret = xTaskCreate(task_lidar, "task_lidar", DEFAULT_STACK_SIZE, NULL, DEFAULT_TASK_PRIORITY+2, &h_task_lidar);
	if(ret != pdPASS)
	{
		printf("Could not create task lidar \r\n");
		Error_Handler();
	}
	ret = xTaskCreate(task_lidar_ISR, "task_lidar_ISR", DEFAULT_STACK_SIZE, NULL, DEFAULT_TASK_PRIORITY+1, &h_task_lidar_ISR);
	if(ret != pdPASS)
	{
		printf("Could not create task lidar ISR \r\n");
		Error_Handler();
	}
	ret = xTaskCreate(task_BT_and_Wire_RX_ISR, "task_BT_and_Wire_RX_ISR", DEFAULT_STACK_SIZE, NULL, DEFAULT_TASK_PRIORITY, &h_task_BT_and_Wire_RX_ISR);
	if(ret != pdPASS)
	{
		printf("Could not create task BT ISR \r\n");
		Error_Handler();
	}
	ret = xTaskCreate(task_BTN_ISR, "task_BTN_ISR", DEFAULT_STACK_SIZE/2, NULL, DEFAULT_TASK_PRIORITY, &h_task_BTN_ISR);
	if(ret != pdPASS)
	{
		printf("Could not create task BTN ISR \r\n");
		Error_Handler();
	}
	ret = xTaskCreate(task_Motor, "task_Motor", DEFAULT_STACK_SIZE, NULL, DEFAULT_TASK_PRIORITY+4, &h_task_Motor);
	if(ret != pdPASS)
	{
		printf("Could not create task Motor \r\n");
		Error_Handler();
	}
	ret = xTaskCreate(task_MotorSpeed, "task_MotorSpeed", DEFAULT_STACK_SIZE, NULL, DEFAULT_TASK_PRIORITY+3, &h_task_MotorSpeed);
	if(ret != pdPASS)
	{
		printf("Could not create task MotorSpeed \r\n");
		Error_Handler();
	}

	/*ret = xTaskCreate(IMU_taskRead, "IMU_taskRead", DEFAULT_STACK_SIZE+50, NULL, DEFAULT_TASK_PRIORITY + 9, &h_IMU_taskRead);
	if(ret != pdPASS)
	{
		printf("Could not create IMU taskRead \r\n");
		Error_Handler();
	}*/






	//IMU_init(&h_imu);

	vTaskStartScheduler();
  /* USER CODE END 2 */

  /* Call init function for freertos objects (in freertos.c) */
  MX_FREERTOS_Init();

  /* Start scheduler */
  osKernelStart();

  /* We should never get here as control is now taken by the scheduler */
  /* Infinite loop */
  /* USER CODE BEGIN WHILE */
	while (1)
	{
    /* USER CODE END WHILE */

    /* USER CODE BEGIN 3 */
	}
  /* USER CODE END 3 */
}

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
/**
  * @brief  Period elapsed callback in non blocking mode
  * @note   This function is called  when TIM6 interrupt took place, inside
  * HAL_TIM_IRQHandler(). It makes a direct call to HAL_IncTick() to increment
  * a global variable "uwTick" used as application time base.
  * @param  htim : TIM handle
  * @retval None
  */
void HAL_TIM_PeriodElapsedCallback(TIM_HandleTypeDef *htim)
{
  if (htim->Instance == TIM6) {
    HAL_IncTick();
  }
  /* USER CODE BEGIN Callback 1 */
	if (htim->Instance == TIM7) {
		odom_overflow++;
		HAL_GPIO_TogglePin(USER_LED0_GPIO_Port, USER_LED0_Pin);
	}
  /* USER CODE END Callback 1 */
}

/**
  * @brief  This function is executed in case of error occurrence.
  * @retval None
  */
void Error_Handler(void)
{
  /* USER CODE BEGIN Error_Handler_Debug */
	HAL_GPIO_WritePin(USER_LED3_GPIO_Port, USER_LED3_Pin, 1);
	/* User can add his own implementation to report the HAL error return state */
	__disable_irq();
	while (1)
	{
	}
  /* USER CODE END Error_Handler_Debug */
}

#ifdef  USE_FULL_ASSERT
/**
  * @brief  Reports the name of the source file and the source line number
  *         where the assert_param error has occurred.
  * @param  file: pointer to the source file name
  * @param  line: assert_param error line source number
  * @retval None
  */
void assert_failed(uint8_t *file, uint32_t line)
{
  /* USER CODE BEGIN 6 */
	/* User can add his own implementation to report the file name and line number,
     ex: printf("Wrong parameters value: file %s on line %d\r\n", file, line) */
  /* USER CODE END 6 */
}
#endif /* USE_FULL_ASSERT */

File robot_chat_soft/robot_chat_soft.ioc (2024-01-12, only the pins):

Mcu.UserName=STM32G070RBTx
PA0.GPIO_Label=BAT_ADC
PA0.Signal=ADC1_IN0
PA13.Signal=SYS_SWDIO
PA14-BOOT0.Signal=SYS_SWCLK
PA2.GPIO_Label=ST_LINK_TX
PA2.Signal=USART2_TX
PA3.GPIO_Label=ST_LINK_RX
PA3.Signal=USART2_RX
PA5.GPIO_Label=BT_TX
PA5.Signal=USART3_TX
PA6.GPIO_Label=R_ENCODE_B
PA6.Signal=S_TIM3_CH1
PA7.GPIO_Label=R_ENCODE_A
PA7.Signal=S_TIM3_CH2
PA8.GPIO_Label=L_ENCODE_B
PA8.Signal=S_TIM1_CH1
PA9.GPIO_Label=L_ENCODE_A
PA9.Signal=S_TIM1_CH2
PB1.GPIO_Label=I_READ_R
PB1.Signal=ADC1_IN9
PB10.GPIO_Label=I_READ_L
PB10.Signal=ADC1_IN11
PB14.GPIO_Label=L_FORWARD
PB14.Signal=S_TIM15_CH1
PB15.GPIO_Label=LIDAR_SPEED
PB15.Signal=S_TIM15_CH2
PB3.GPIO_Label=IMU_SPI_CLK
PB3.Signal=SPI1_SCK
PB4.GPIO_Label=IMU_SPI_CS
PB4.Signal=GPIO_Output
PB6.GPIO_Label=USER_LED0
PB6.Signal=GPIO_Output
PB7.GPIO_Label=USER_LED1
PB7.Signal=GPIO_Output
PB8.GPIO_Label=USER_LED2
PB8.Signal=GPIO_Output
PB9.GPIO_Label=USER_LED3
PB9.Signal=GPIO_Output
PC0.GPIO_Label=BUMP_EXTI
PC0.Signal=GPXTI0
PC1.GPIO_Label=FBD_EXTI
PC1.Signal=GPXTI1
PC10.GPIO_Label=USER_LED4
PC10.Signal=GPIO_Output
PC11.GPIO_Label=BT_RX
PC11.Signal=USART3_RX
PC12.GPIO_Label=R_FORWARD
PC12.Signal=S_TIM14_CH1
PC13.GPIO_Label=BTN_GAME_STATUS
PC13.Signal=GPXTI13
PC2.GPIO_Label=BBD_EXTI
PC2.Signal=GPXTI2
PC4.GPIO_Label=LIDAR_TX
PC4.Signal=USART1_TX
PC5.GPIO_Label=LIDAR_RX
PC5.Signal=USART1_RX
PC6.GPIO_Label=LIDAR_EN
PC6.Signal=GPIO_Output
PC7.GPIO_Label=LIDAR_RANGING_EN
PC7.Signal=GPIO_Output
PD0.GPIO_Label=L_REVERSE
PD0.Signal=S_TIM16_CH1
PD1.GPIO_Label=R_REVERSE
PD1.Signal=S_TIM17_CH1
PD3.GPIO_Label=IMU_INT1
PD3.Signal=GPXTI3
PD4.GPIO_Label=IMU_INT2
PD4.Signal=GPXTI4
PD5.GPIO_Label=IMU_SPI_SDO
PD5.Signal=SPI1_MISO
PD6.GPIO_Label=IMU_SPI_SDI
PD6.Signal=SPI1_MOSI

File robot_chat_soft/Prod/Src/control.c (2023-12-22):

#include "control.h"
#include "fixpoint_math.h"

/**
  * @brief Motor speed control loop, this function should be called right after odometry_update_pos()
  * @param *hMotor : address of motor structure containing motor parameters.
  *	@retval None
  */
void set_speed_PID(hMotor_t * hMotor,int32_t input)
{
	hMotor->speed_error[hMotor->speed_index] = input - hMotor->speed_measured[hMotor->speed_index];

	hMotor->speed_integral += hMotor->speed_anti_windup*(hMotor->speed_error[(hMotor->speed_index + 2)%3] + hMotor->speed_error[hMotor->speed_index]);

	hMotor->speed_anti_windup = 1;

	hMotor->speed_output[hMotor->speed_index] = fixed_mul_16(hMotor->speed_error[hMotor->speed_index], (int32_t)hMotor->speed_corr_params[0]) +
												fixed_mul_16(hMotor->speed_integral, (int32_t)hMotor->speed_corr_params[1]) +
												fixed_mul_16(hMotor->speed_measured[(hMotor->speed_index + 2)%3] - hMotor->speed_measured[hMotor->speed_index], (int32_t)hMotor->speed_corr_params[2]) +
												fixed_mul(input,5<<12,16) /*hMotor->speed_output[(hMotor->speed_index + 2)%3] /*+
												fixed_mul_16(hMotor->speed_error[(hMotor->speed_index + 2)%3], (hMotor->speed_corr_params[1] - hMotor->speed_corr_params[2])*2) +
												fixed_mul_16(hMotor->speed_error[(hMotor->speed_index + 1)%3], hMotor->speed_corr_params[1] + hMotor->speed_corr_params[2] - hMotor->speed_corr_params[0]) +
												hMotor->speed_output[(hMotor->speed_index - 2)%3]*/;

	//Current saturation based on the difference between drive voltage and BEMF,
	//prevents OCD triggering, which can cause a motor to stall and never ramp up again

	if(fixed_div(hMotor->speed_output[hMotor->speed_index],128<<16,16) - fixed_div(hMotor->speed_measured[hMotor->speed_index],80<<16,16) > 1<<18)
	{
		hMotor->speed_output[hMotor->speed_index] = fixed_mul(fixed_div(hMotor->speed_measured[hMotor->speed_index],80<<16,16) + (1<<18), 128<<16, 16);
		hMotor->speed_anti_windup = 0;
	}
	else if(fixed_div(hMotor->speed_output[hMotor->speed_index],128<<16,16) - fixed_div(hMotor->speed_measured[hMotor->speed_index],80<<16,16) < -1<<18)
	{
		hMotor->speed_output[hMotor->speed_index] = fixed_mul(fixed_div(hMotor->speed_measured[hMotor->speed_index],80<<16,16) - (1<<18), 128<<16, 16);
		hMotor->speed_anti_windup = 0;
	}

	//PWM saturation

	if(hMotor->speed_output[hMotor->speed_index] > (int32_t)hMotor->speed_corr_params[3])
	{
		hMotor->speed_output[hMotor->speed_index] = (int32_t)hMotor->speed_corr_params[3];
		hMotor->speed_anti_windup = 0;

	}
	else if(hMotor->speed_output[hMotor->speed_index] < -1*((int32_t)hMotor->speed_corr_params[3]))
	{
		hMotor->speed_output[hMotor->speed_index] = -1*((int32_t)hMotor->speed_corr_params[3]);
		hMotor->speed_anti_windup = 0;
	}
	motor_set_PWM(hMotor, hMotor->speed_output[hMotor->speed_index]/(1<<16));
	hMotor->speed_index = (hMotor->speed_index + 1) % 3;
	//TODO fully implement feedforward
}

int32_t error_old = 0;
int32_t integral = 0;
int32_t anti_windup = 1;
/**
  * @brief Angular position control loop, this function should be called regularly.
  * TODO implement full corrector
  * @param *hMotor : address of motor structure containing motor parameters.
  *	@retval diff : return L/R speed coefficient
  */
int32_t set_angle_corr(hOdometry_t * hOdometry, int32_t input)
{
	int32_t output = 0; //Q7.24
	int32_t error = modulo_2pi(input - hOdometry->angle); //Q7.24
	integral += anti_windup*error/10;
	anti_windup = 1;
	//printf("a_err = %d\r\n",10*(int)hOdometry->angle/(1<<24));

	output = 5*error - 15*(hOdometry->angle - error_old);
	error_old = hOdometry->angle;

	if(output > 1<<23)
	{
		anti_windup = 0;
	}
	else if(output < -1<<23)
	{
		anti_windup = 0;
	}
	return fixed_mul(Arctan(output/(1<<8)),INV_PI,23);
	//return output;
}

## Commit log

2023-09-18 BOM v1
    [BOM.xlsx]
2023-09-19 PIN CubeIDE et PCB
    [BOM.xlsx, captors.kicad_sch, motor_drivers.kicad_sch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]
2023-09-20 ajout BOM v2
    [BOM.xlsx]
2023-09-20 pcb alim et connecteurs
    [BOM.xlsx, captors.kicad_sch, power_supply.kicad_sch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]
2023-09-21 Ajout lecture courant et enable lidar sur ioc
    [BOM.xlsx, captors.kicad_sch, motor_drivers.kicad_sch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]
2023-09-21 Modif PCB
    [HMI.kicad_sch, NCS199A3RSQT2G.stp, captors.kicad_sch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]
2023-09-22 Ajout IMU
2023-09-22 Ajout IMU pcb
    [HMI.kicad_sch, NCS199A3RSQT2G.stp, captors.kicad_sch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]
2023-09-25 Labels non reliés pour BOM
    [HMI.kicad_sch, NCS199A3RSQT2G.stp, captors.kicad_sch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]
2023-09-25 PCB revu
    [HMI.kicad_sch, NCS199A3RSQT2G.stp, STP_472 121 020 421 (rev1).stp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]
2023-09-25 ajout BOM
    [HMI.kicad_sch, NCS199A3RSQT2G.stp, STP_472 121 020 421 (rev1).stp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]
2023-09-25 PCB final avec BOM
    [HMI.kicad_sch, NCS199A3RSQT2G.stp, STP_472 121 020 421 (rev1).stp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]
2023-09-28 Placement composants
    [robot_chat.kicad_pcb, robot_chat.kicad_sch]
2023-10-02 Mise à jour placement
    [HMI.kicad_sch, captors.kicad_sch, motor_drivers.kicad_sch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]
2023-10-02 changed Rsense position
    [HMI.kicad_sch, captors.kicad_sch, motor_drivers.kicad_sch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]
2023-10-03 Mise à jour led bumper
    [captors.kicad_sch, robot_chat.kicad_pcb]
2023-10-05 Lidar data extracted
2023-10-06 Lidar data computing
2023-10-09 Nom des fonctions & variables changé de ylidar à ydlidar
2023-10-09 Routage final v1
    [robot_chat.kicad_pcb]
2023-10-09 routage final v1.1
    [robot_chat.kicad_pcb, stm.kicad_sch]
2023-10-09 correct lidar lib and adding lidar visualizer
    [lidar_dev.ioc, lidar_visualizer_Processing43.pde, main.c]
2023-10-16 Routage final v1.2
    [motor_drivers.kicad_sch, power_supply.kicad_sch, robot_chat.kicad_pcb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]
2023-10-16 adding encoder test project
2023-10-26 fixed DRC, added html bom
    [HMI.kicad_sch, captors.kicad_sch, motor_drivers.kicad_sch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]
2023-11-01 nom plus simple dans le main de variable de structure et re-ajout des distances sur 360 deg avec un choix ifdef
2023-11-01 simplifying variable name in function by lidar instead of ydlidar_x4
2023-11-13 test MCU avec freetos et test user led ok
2023-11-13 ajout du BT pour le print
2023-11-13 Start of IMU driver
2023-11-13 IMU dev init
2023-11-13 ajout lidar en cours, ajouter l'etape de calcule
2023-11-22 reception et envoie des donnees lidar utilisable
2023-11-23 SPI communicant
2023-11-23 lidar ok sans DMA pour linstant
2023-11-29 improving lidar dev demo stability
    [lidar_dev.ioc, lidar_visualizer_Processing43.pde, main.c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]
2023-11-29 lidar ok sur PCB robot chat
2023-12-01 lidar ok pour PCB chat
2023-12-01 Fonction de lecture et d'écriture d'un registre
2023-12-01 Rebase de ajout moteur
2023-12-02 Boucle de lecture de rotation et tache de printf
2023-12-02 added motor driver
2023-12-02 added motor speed and current sensing
2023-12-03 fixed current sensing, added battery voltage sensing
    [main.c, motor.c, robot_chat_code.ioc]
2023-12-04 added fixed point math and speed PID V1
    [control.c, main.c, motor.c]
2023-12-08 lidar ok avec moteur
2023-12-10 added odometry, changed PID frequency and parameters
2023-12-10 fixed OCD triggering and deadlock issue
    [control.c, main.c, robot_chat_code.ioc]
2023-12-10 added angular control, fixed odometry
    [control.c, main.c, odometry.c]
2023-12-11 Fin 1ere phase programmation IMU
2023-12-11 IMU merge ok
2023-12-13 IOC modifie et ajout var de strategie
2023-12-13 Suppression des .metadata du repo
2023-12-13 modif pour lidar
2023-12-13 lidar ok for old project
2023-12-13 Debut fonction de strategie et champ vectoriel
2023-12-13 lidar almost working
2023-12-14 Correction conflits init et prototypes de fonctions
2023-12-14 Champ vectoriel avec un offset unique pour tous les cotes (necessaire pour les courbes de suivi circulaires)
2023-12-14 Utilisation des fonctions * et / en virgule fixe
2023-12-18 Fonctions de champ de vect implementes
2023-12-18 Suivi de courbe lineaire implemente, la correction d'ecartement fonctionne
2023-12-18 Cas de chute et collision implementes
2023-12-19 lidar tracking
2023-12-19 Commande de suivi de ligne a tester
2023-12-19 move to new project, lidar tracking bugfix
    [control.c, imu.c, main.c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]
2023-12-20 Printf par interruption fonctionnel
2023-12-20 Probleme d'overflow de l'odom regle, strat a tester sur le robot
    [config.h, control.c, main.c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]
2023-12-20 patched odometry overflow
2023-12-21 Vecteur de consigne fiable (sans overflow) et printf en DMA
2023-12-21 simplification code concernant les angles start et end
2023-12-22 fction init du lidar ok
2023-12-22 Prise en compte des bumpers et capteurs de chute dans la stratégie

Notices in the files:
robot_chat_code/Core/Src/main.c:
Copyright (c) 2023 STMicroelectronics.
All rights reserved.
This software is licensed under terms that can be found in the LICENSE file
